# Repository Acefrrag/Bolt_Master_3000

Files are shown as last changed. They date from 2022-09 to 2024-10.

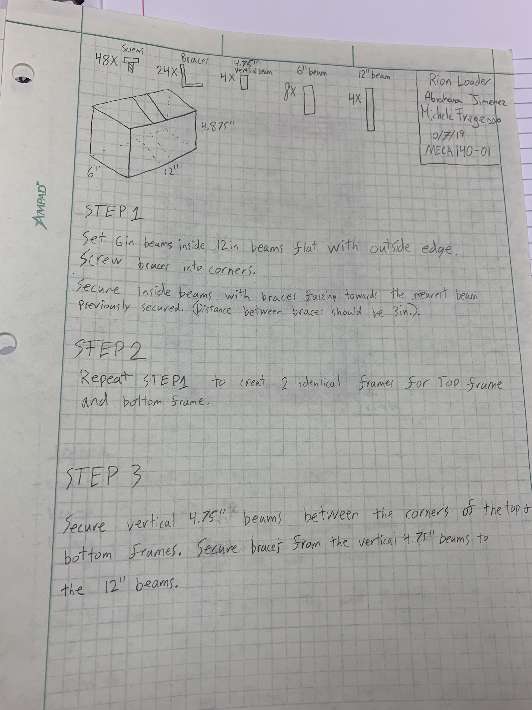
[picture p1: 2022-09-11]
Documentation/IMG_3115.jpg

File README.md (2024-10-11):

# Bolt Master 3000

## Repository Description
This github repositories collects all the documentation(CAD files, reports, BOMs, brainstorming notes) produced during the design and development of a proof-of-concept mechatronic system for the undergraduatee course **MECA140 - Introduction to Engineering Design and Automation** during A.Y. 2019-2020.

## Project Description

The aim of the proof-of-concept system was to explore ways to automatize the process of checking proper bolt installation on a generic structure.

The proof-of-concept system objective is to test the proper installation of 4 bolts in 1/4-20 holes on a 4-by-4-inch-area stainless steel plate. The system ensures bolt preload is present on all of them, and warns the user if a bolt is missing or not tightly screwed.

My team designed the Bolt Master 3000. This PLC-controlled system includes the OMRON NX1P2, which controls the actuation and the sensing system. 

### Working princple
The bolt is checked by pushing a DC motors onto it using a pneumatic actuator. The DC motor shaft is coupled with with a universal socket to successfully target the bolt cap. The DC motor starts applying a torque on the bolt and, depending on the amount of current drained from the power supply (measured with a shunt resistor), the controller is able to tell wheather the bolt is there or not.

Here is a demo of the system where it shows the system testing a correctly installed bolt and a missing bolt.

https://user-images.githubusercontent.com/59066474/189550218-b4baf25a-3ad1-4a13-9e47-b2368a44c600.mp4

The user interface on the screen has a button to start the bolt testing. The user interface displays the result with a pair of LEDs per bolt(RED for failure, GREEN for success). Neverthless, as it can be seen the user interface implemented included only 2 bolt. There was a lack of actuators and ther is only one DC motor testing unit. The corresponind is diplayed on the top right.

1. In the first test there is no bolt installed in the hole. As the motor spins, the amount of current drained is the lowest, therefore the system detects there is no bolt. The result is marked with a RED flag on the PLC monitor, aknowledging the failure in the installation of the bolt.
2. In the second test the bolt has been correctly installed. In this case as the voltage at the DC motor ends, the motor doesn't spin draining a much greater amount of current. In this case, the system detects a bolt and the corresponding GREEN LED light up.

## Team 

The project is the result of the team work with my teammates Rion Loader and Abrham Jimenez.

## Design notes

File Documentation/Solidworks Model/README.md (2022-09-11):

## Description of Solidworks Models

This folder includes the CAD files of Bolt Master 3000. The frame has 2 versions

1. Version 1.0. Originally made
2. Version 1.1. This version include an additional extruder on the top to support the descending plate.

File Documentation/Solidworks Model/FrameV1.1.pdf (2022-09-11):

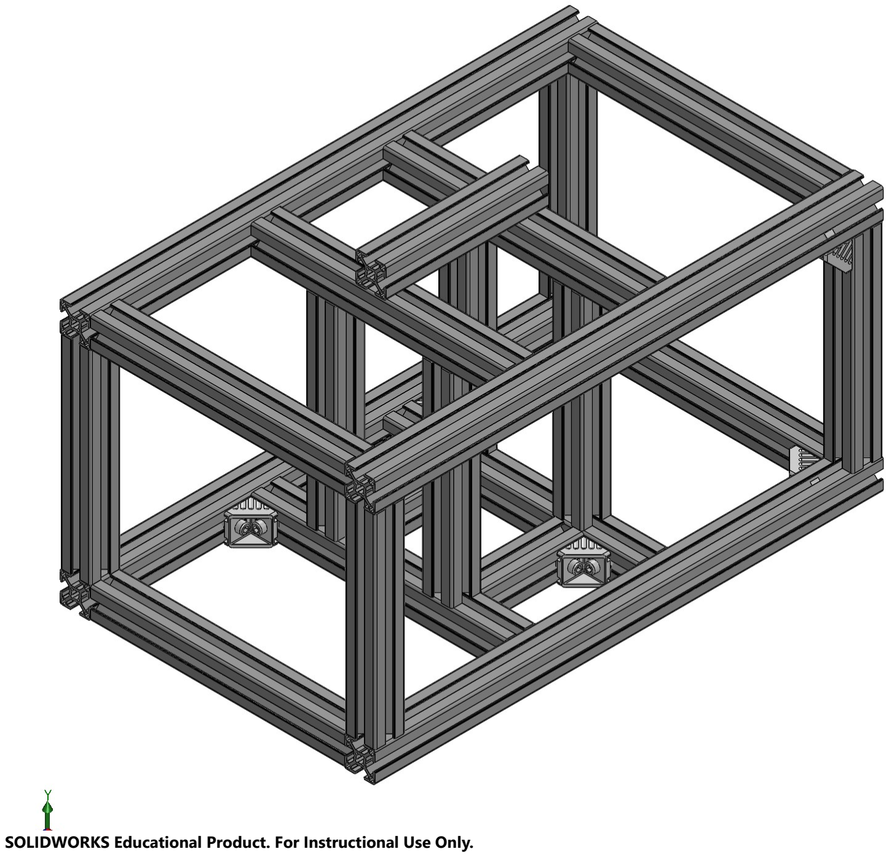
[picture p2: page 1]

SOLIDWORKS Educational Product. For Instructional Use Only.

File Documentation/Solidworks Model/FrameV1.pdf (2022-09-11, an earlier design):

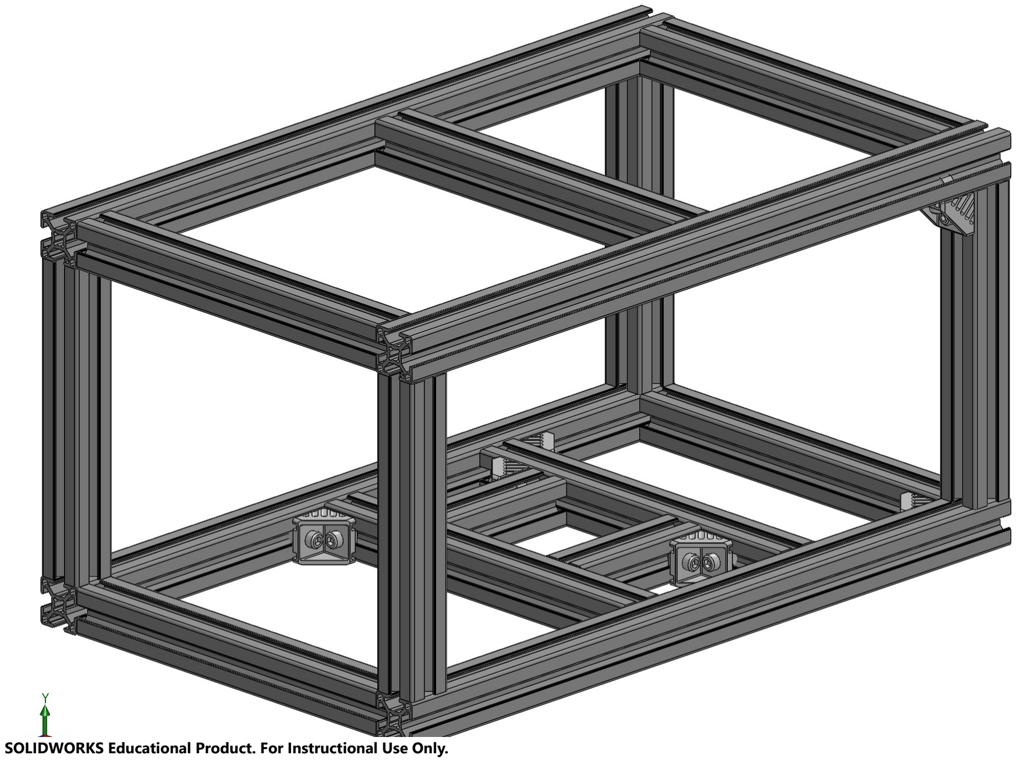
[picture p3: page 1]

SOLIDWORKS Educational Product. For Instructional Use Only.

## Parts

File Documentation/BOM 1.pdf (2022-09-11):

Quantity | Manufacturer | P/N | Description | Length | Tolerance | Special Conditions | Cost | Vendor | Vender #
4 | Bosch-Rexoth | LA1 | Long arm for frame | 500mm | ±20mm | N/A | | CSU | (530)898-5129
16 | Bosch-Rexoth | SA1 | Short arm for frame | 250mm | ±0mm | Has to be exact | | CSU | (530)898-5129
2 | Bosch-Rexoth | SA2 | Short arm for support 1 | 100mm | ±0mm | Has to be exact | | CSU | (530)898-5129
1 | Bosch-Rexoth | SA3 | Short arm for support 1 | 100mm | ±20mm | N/A | | CSU | (530)898-5129
1 | Bosch-Rexoth | SA4 | Short arm for support 1 | 250mm | ±20mm | N/A | | CSU | (530)898-5129
1 | Omron | NX1P2 | PLC | N/A | N/A | N/A | | CSU | (530)898-5129
1 | B&R Automation | 4PP035.0300-36 | Controller | N/A | N/A | N/A | | CSU | (530)898-5129
1 | | | Power Supply | N/A | N/A | N/A | | CSU | (530)898-5129
1 | Aplied Motion Products | ST5-Si | DC Motor | N/A | N/A | N/A | | CSU | (530)898-5129
1 | SMC | NAW2000- | Dual Filter/Regulator | N/A | N/A | N/A | | CSU | (530)898-5129
1 | SMC | NVZ1120-5L0-M5 | Solenoid Block | N/A | N/A | N/A | | CSU | (530)898-5129
1 | SMC | NCME075-0400 | Actuator | N/A | N/A | N/A | | CSU | (530)898-5129
1 | Gator Grip | ETC120 | Universal Socket | N/A | N/A | N/A | $5.00 | asseenontv.com | 800-7269411
1 | In House | P1 | Plate Top | 100 x 100 (mm) | ±0mm | Has to be exact | N/A | N/A | N/A
1 | In House | P2 | Plate Bottom | 120 x 120 (mm) | ±0mm | Has to be exact | N/A | N/A | N/A
B. O. M.

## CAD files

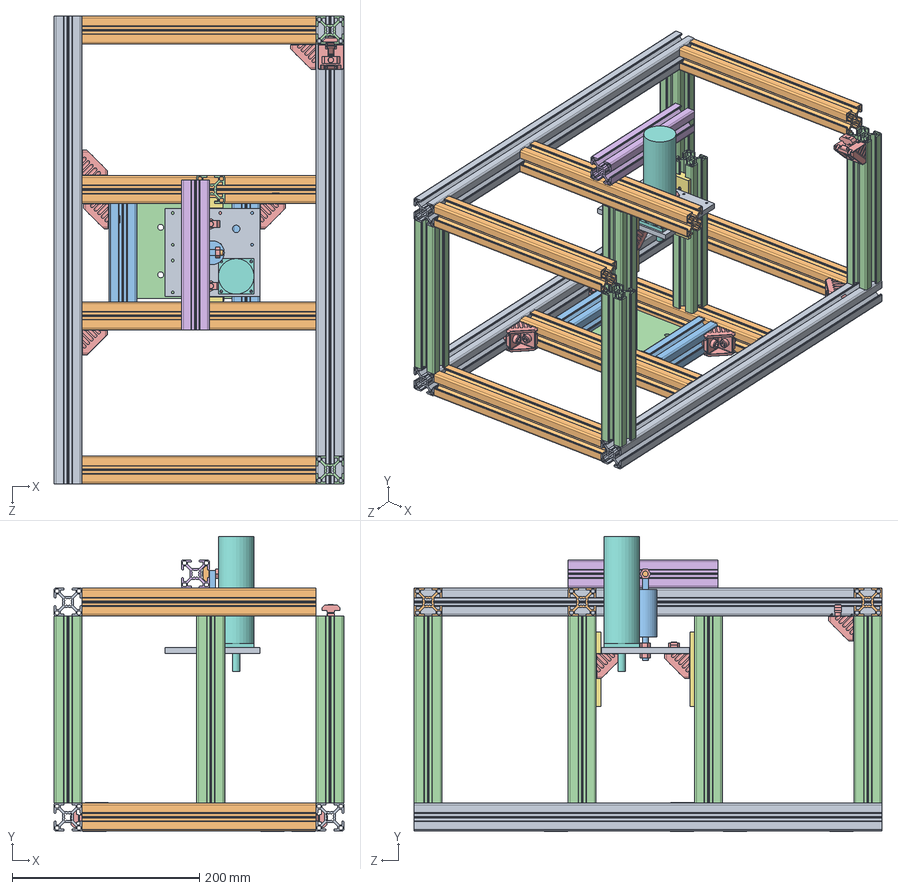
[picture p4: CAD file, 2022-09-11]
Documentation/Solidworks Model/Soliworks Parts/Frame_V1.1.SLDASM
310.0 x 315.5 x 500.0 mm
LBV1 x 3
SBV1 x 7
SBV2 x 2
VBV1 x 6
Rexroth-3 842 523 530 x 8
SBV3
slide bearing for 8mm T-slots, flat x 2
Motor
Moving_Plate
Connection
Pneumetic
Plate
Nut x 5

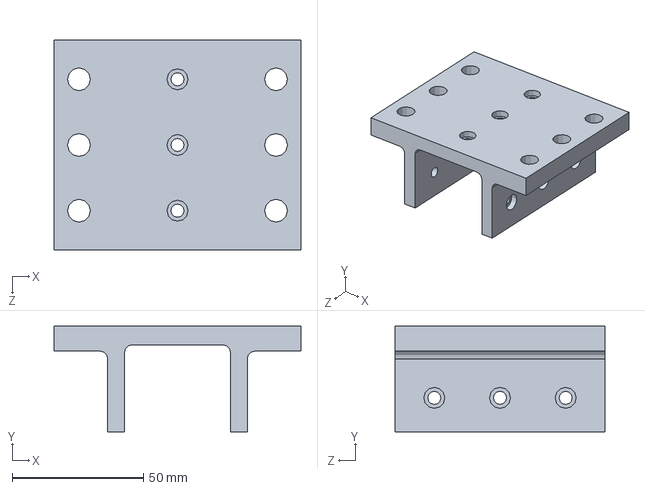
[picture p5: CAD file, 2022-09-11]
Documentation/Solidworks Model/Soliworks Parts/30x30x80 mm EcoSlide carriage.SLDPRT
94.0 x 40.3 x 80.0 mm

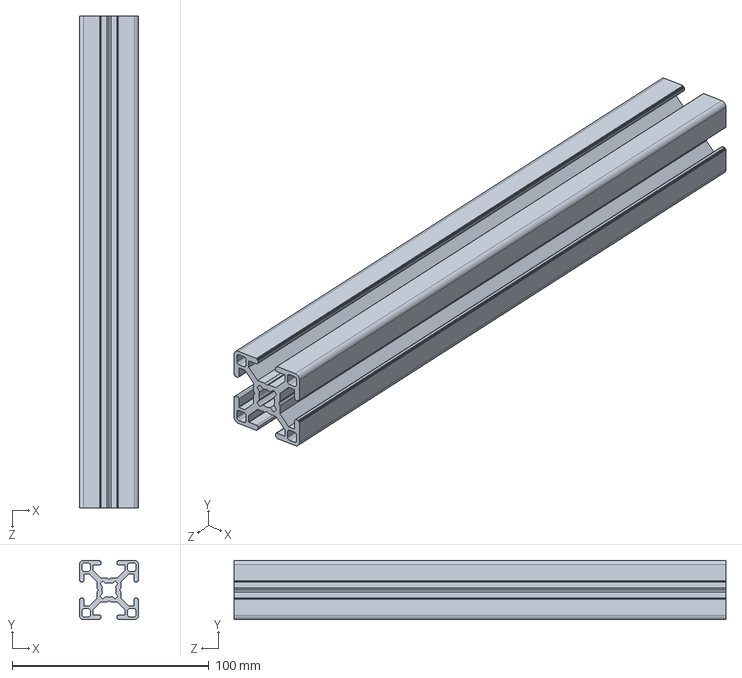
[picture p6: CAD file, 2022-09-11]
Documentation/Solidworks Model/Soliworks Parts/SBV1.SLDPRT
30.0 x 30.0 x 250.0 mm

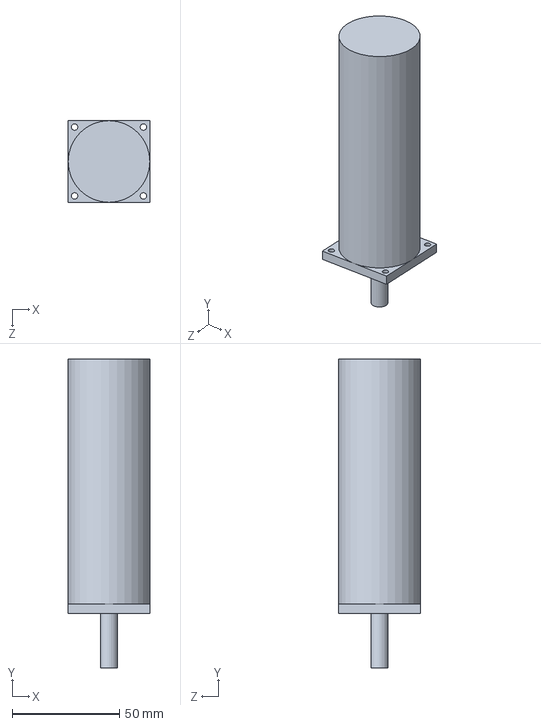
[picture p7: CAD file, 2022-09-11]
Documentation/Solidworks Model/Soliworks Parts/Motor.SLDPRT
38.1 x 144.1 x 38.1 mm

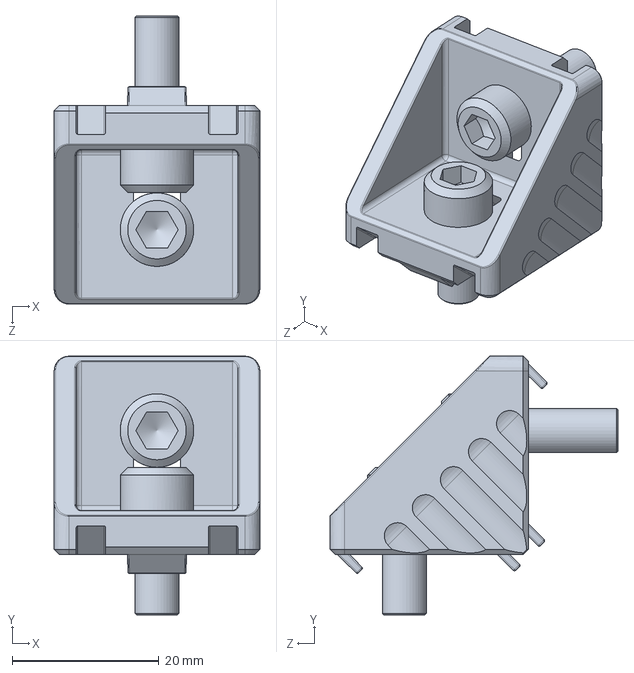
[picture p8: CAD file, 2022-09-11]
Documentation/Solidworks Model/Soliworks Parts/Rexroth-3 842 523 530.SLDPRT
28.0 x 35.2 x 39.2 mm

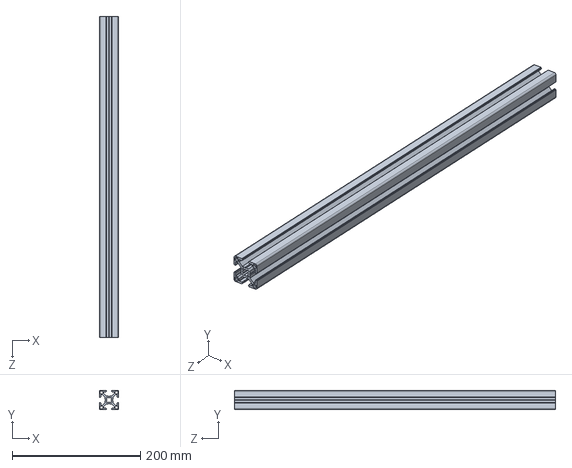
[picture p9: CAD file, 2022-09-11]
Documentation/Solidworks Model/Soliworks Parts/LBV1.SLDPRT
30.0 x 30.0 x 500.0 mm

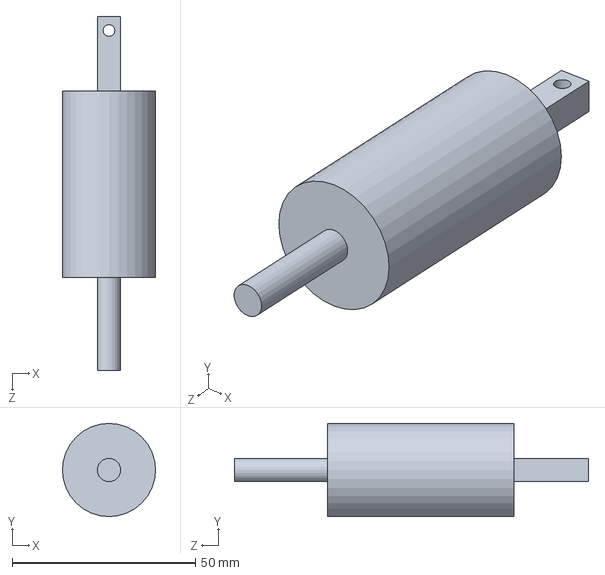
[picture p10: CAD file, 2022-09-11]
Documentation/Solidworks Model/Soliworks Parts/Pneumetic.SLDPRT
25.4 x 25.4 x 96.5 mm

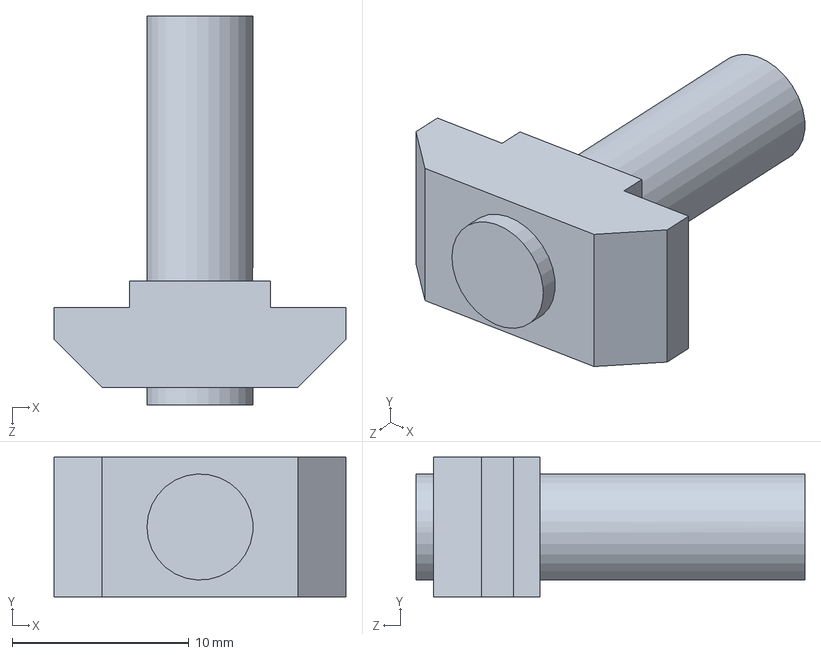
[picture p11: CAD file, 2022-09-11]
Documentation/Solidworks Model/Soliworks Parts/Connection.SLDPRT
16.5 x 7.90 x 22.0 mm

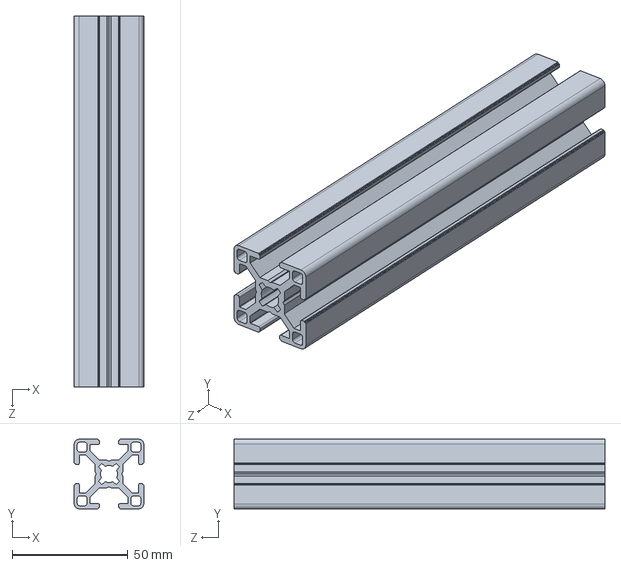
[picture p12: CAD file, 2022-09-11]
Documentation/Solidworks Model/Soliworks Parts/SBV3.SLDPRT
30.0 x 30.0 x 160.0 mm

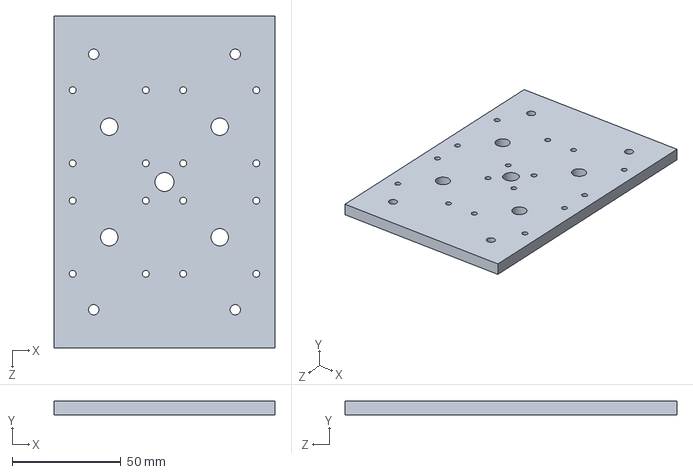
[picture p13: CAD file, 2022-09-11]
Documentation/Solidworks Model/Soliworks Parts/Moving_Plate.SLDPRT
101.6 x 6.35 x 152.4 mm

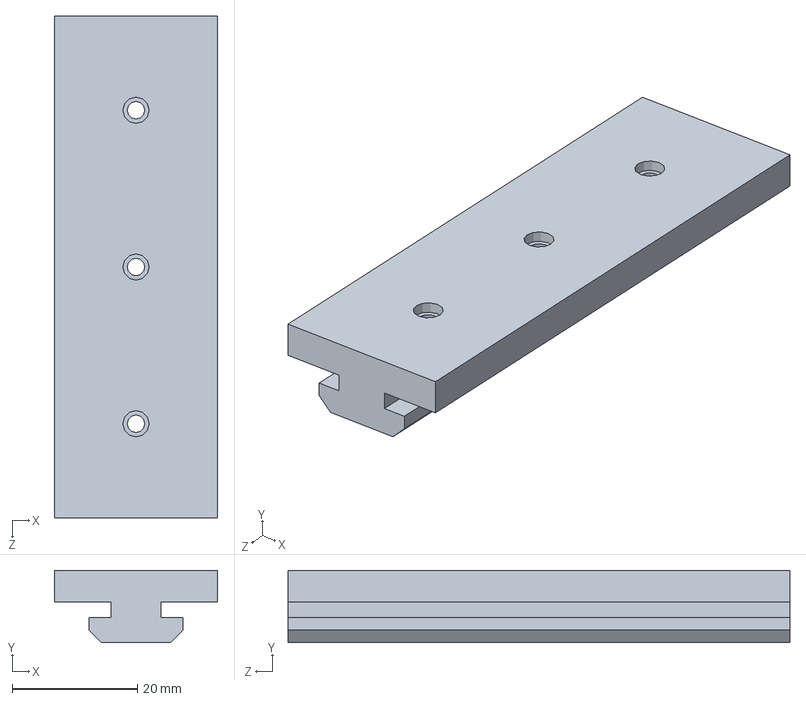
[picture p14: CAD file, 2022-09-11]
Documentation/Solidworks Model/Soliworks Parts/slide bearing for 8mm T-slots, flat.SLDPRT
26.0 x 11.5 x 80.0 mm

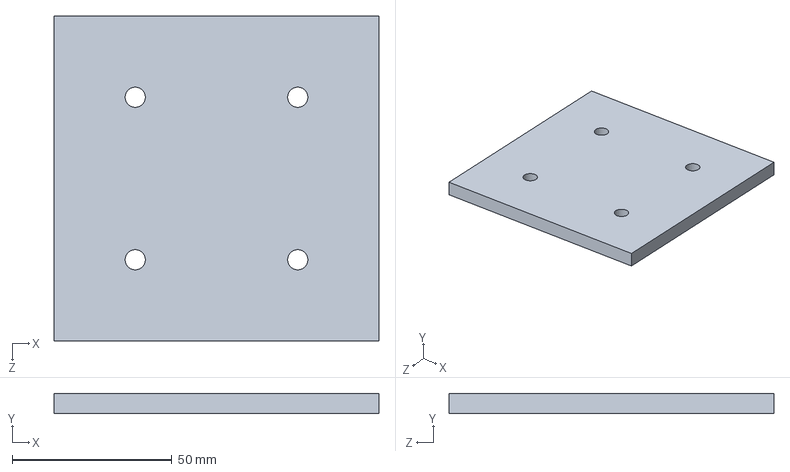
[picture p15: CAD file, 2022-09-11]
Documentation/Solidworks Model/Soliworks Parts/Plate.SLDPRT
101.6 x 6.35 x 101.6 mm

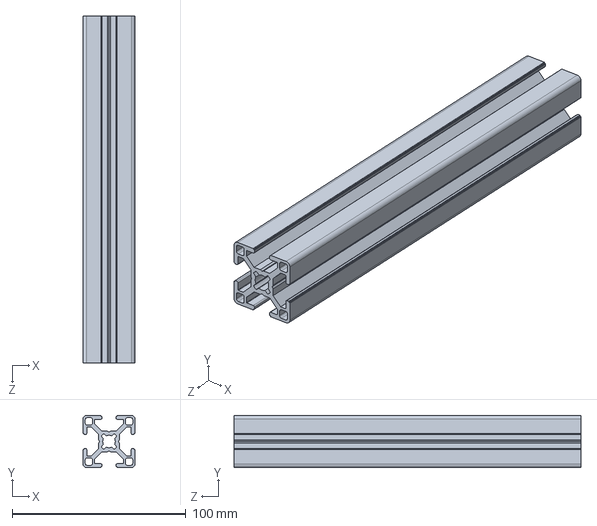
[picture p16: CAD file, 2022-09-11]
Documentation/Solidworks Model/Soliworks Parts/VBV1.SLDPRT
30.0 x 30.0 x 200.0 mm

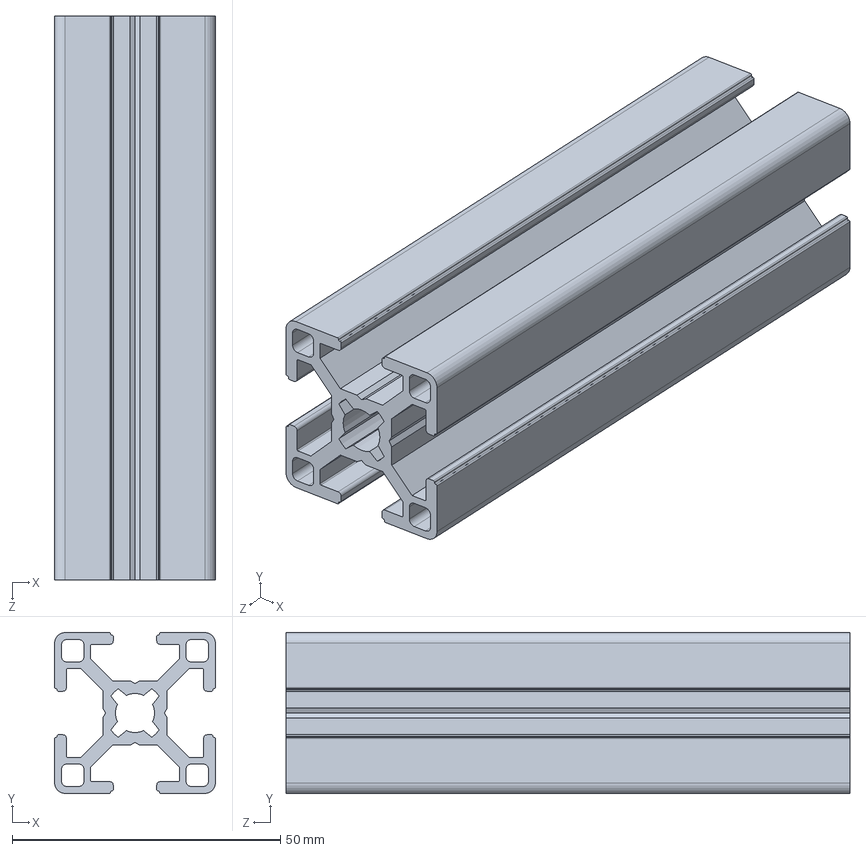
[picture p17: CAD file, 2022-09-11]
Documentation/Solidworks Model/Soliworks Parts/SBV2.SLDPRT
30.0 x 30.0 x 105.0 mm

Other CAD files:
Documentation/Solidworks Model/Soliworks Parts/Rexroth-3 842 990 720_200MM.SLDPRT
Documentation/Solidworks Model/Soliworks Parts/Nut.SLDPRT
Documentation/Solidworks Model/Soliworks Parts/Frame_V1.SLDASM
Documentation/Solidworks Model/Soliworks Parts/Frame_V1.1.SLDDRW
Documentation/Solidworks Model/Soliworks Parts/Moving_Plate.SLDDRW
Documentation/Solidworks Model/Soliworks Parts/Rexroth-3 842 523 530.slddrw
Documentation/Solidworks Model/Soliworks Parts/Rexroth-3 842 990 720_200MM.slddrw

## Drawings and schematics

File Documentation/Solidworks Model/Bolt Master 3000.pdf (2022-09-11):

D

# DETAIL E

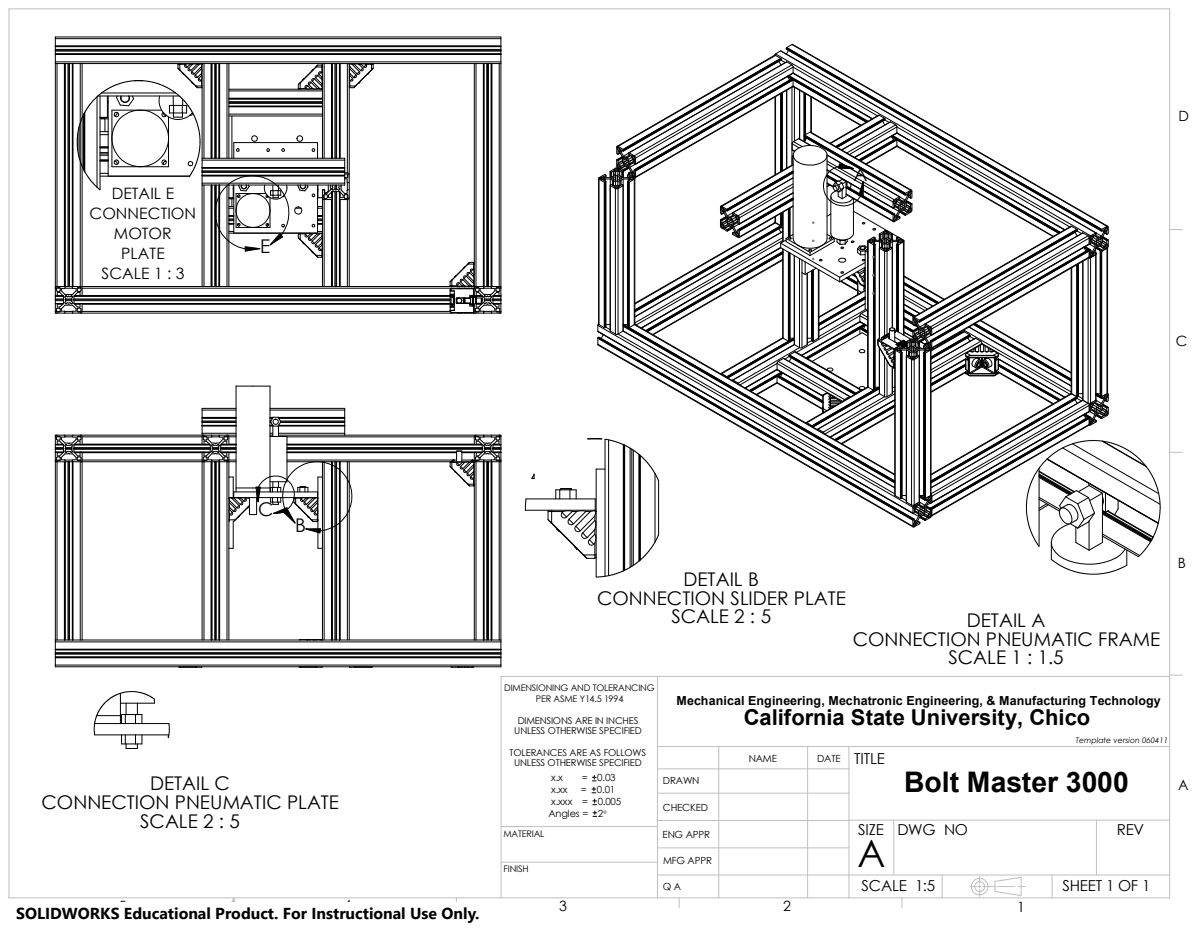
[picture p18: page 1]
FINISH; MATERIAL; x.xx = 0.01 x.xxx = 0.005 Angles = 2; Template version 060411; DETAIL C; SCALE 2 : 5; DETAIL B; DETAIL A; SCALE 1 : 1.5; CONNECTION MOTOR PLATE SCALE 1 : 3

CONNECTION SLIDER PLATE

CONNECTION PNEUMATIC FRAME

DIMENSIONING AND TOLERANCING
PER ASME Y14.5 1994

Mechanical Engineering, Mechatronic Engineering, & Manufacturing Technology
California State University, Chico

DIMENSIONS ARE IN INCHES
UNLESS OTHERWISE SPECIFIED

TOLERANCES ARE AS FOLLOWS

NAME | DATE | TITLE Bolt Master 3000

DRAWN

CONNECTION PNEUMATIC PLATE

CHECKED
ENG APPR | | | SIZE A | DWG NO | REV

MFG APPR
Q A | | | SCALE 1:5 | | | SHEET 1 OF 1

SOLIDWORKS Educational Product. For Instructional Use Only.

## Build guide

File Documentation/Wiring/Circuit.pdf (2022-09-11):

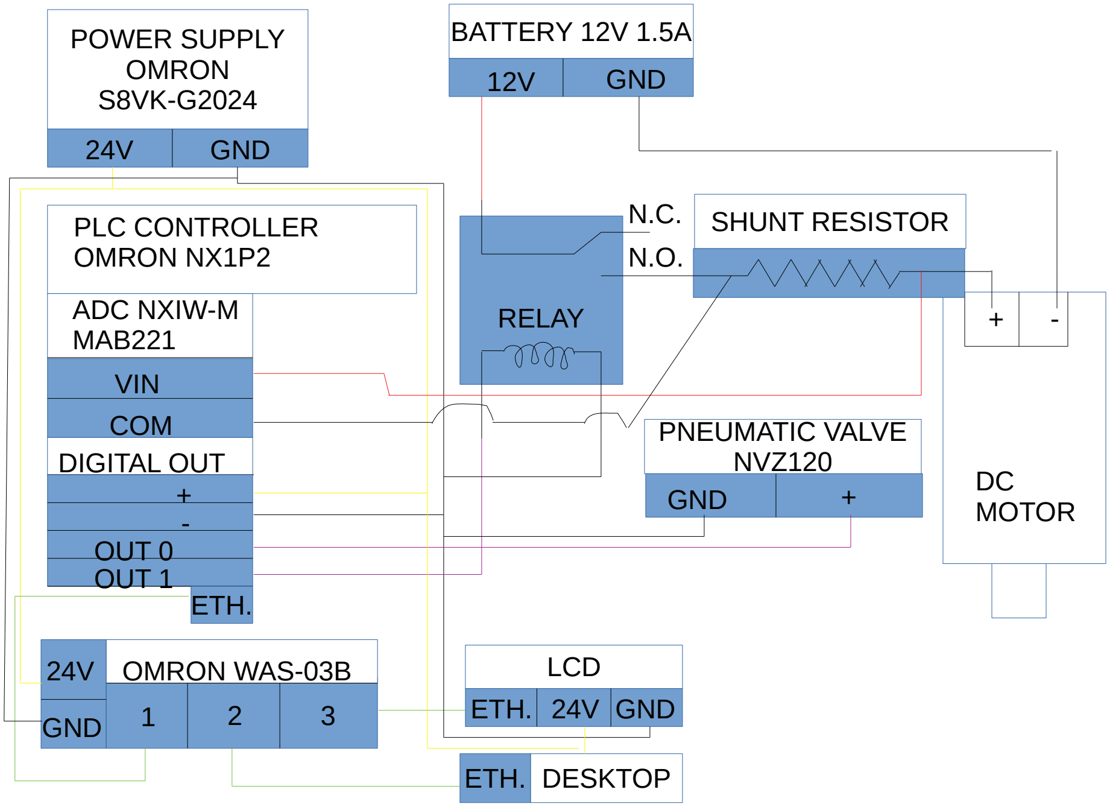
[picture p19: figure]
RELAY; BATTERY 12V 1.5A; GND; DC MOTOR; POWER SUPPLY OMRON S8VK-G2024; SHUNT RESISTOR; PNEUMATIC VALVE NVZ120; ETH.; DESKTOP; PLC CONTROLLER OMRON NX1P2; ADC NXIW-M MAB221 VIN COM DIGITAL OUT + -; OUT 0 OUT 1; OMRON WAS-03B; LCD

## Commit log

2022-09-11 Uploaded first files and added README.md file
    [30x30x80 mm EcoSlide carriage.SLDPRT, Connection.SLDPRT, Frame_V1.1.SLDASM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]
2022-09-11 Added README.md file to CAD folder
    [30x30x80 mm EcoSlide carriage.SLDPRT, Connection.SLDPRT, Frame_V1.1.SLDASM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]
2022-09-11 Verifying local is synche with remote repository
    [BOM 1.xlsx]
2022-09-11 Deleting missplaced files
    [30x30x80 mm EcoSlide carriage.SLDPRT, Connection.SLDPRT, Frame_V1.1.SLDASM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]
